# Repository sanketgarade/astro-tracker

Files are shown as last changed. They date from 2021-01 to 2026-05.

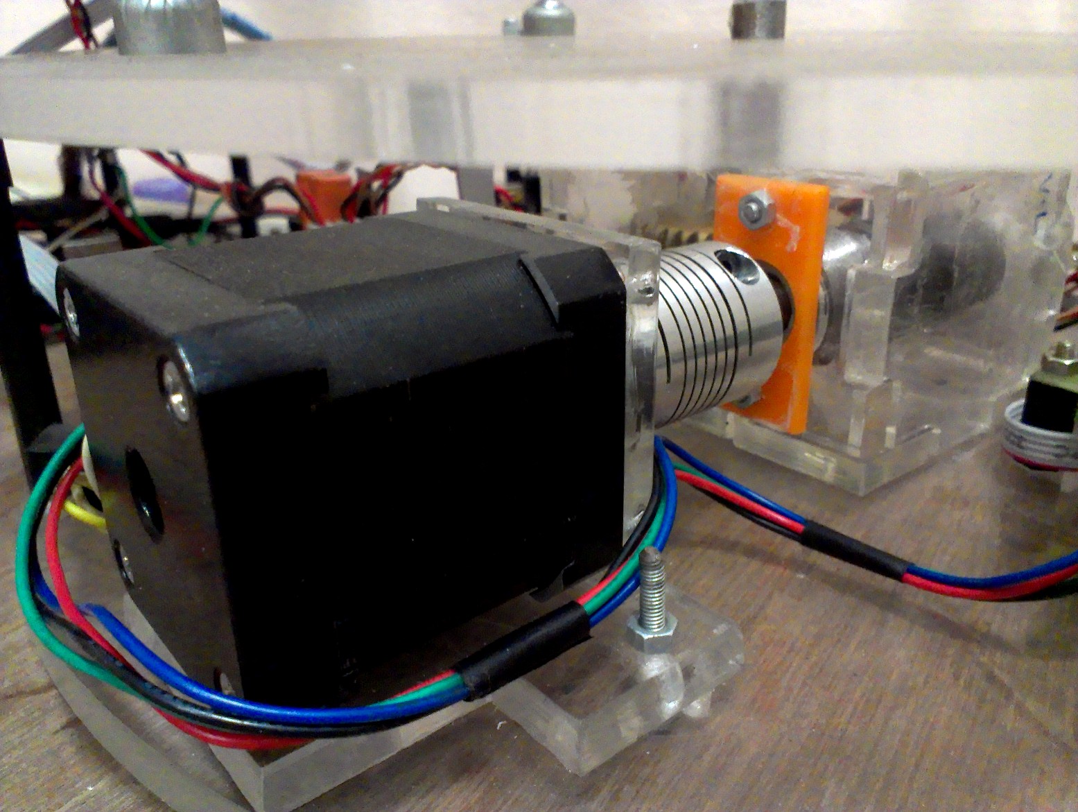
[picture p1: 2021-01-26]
Mechanical/Photos/H_01.jpg

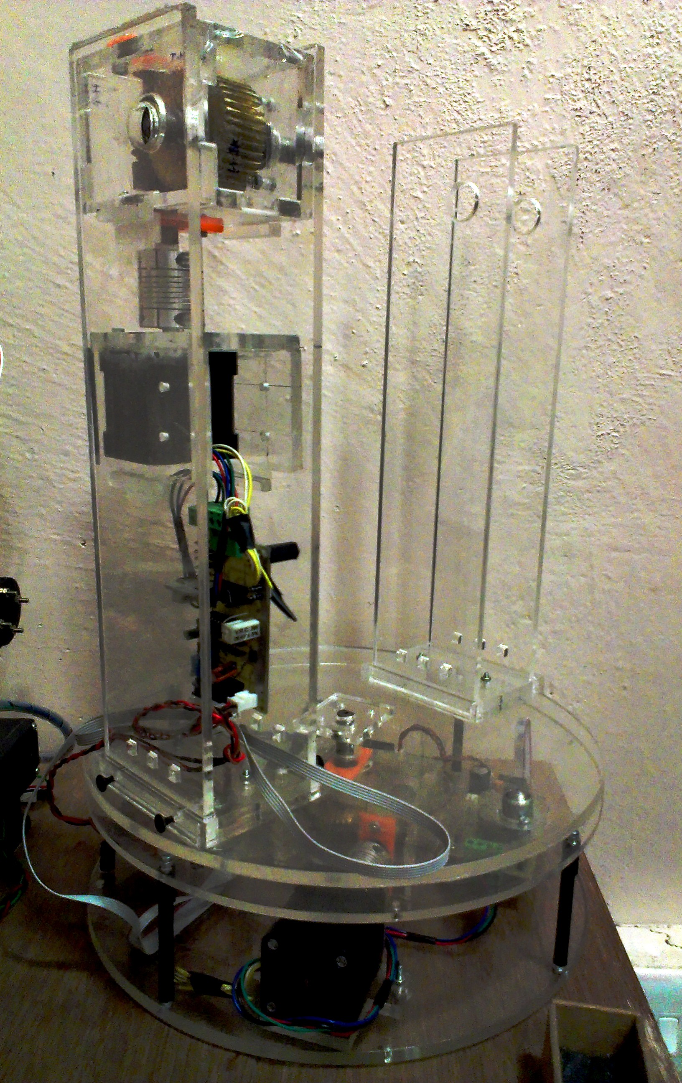
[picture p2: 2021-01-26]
Mechanical/Photos/Full.jpg

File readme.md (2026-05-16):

# Astro Tracker
## Computer controlled alt-az telescope mount

This is my M. Tech. Mechatronics project data. It was done in 2014-15.

Use the **Reports** folder to begin.

In other folders you can find all the documents and files for firmware code, hardware and mechanical CAD files, development plan etc.

## Some images/diagrams from the report are shown for a quick idea of the project



---



---



---



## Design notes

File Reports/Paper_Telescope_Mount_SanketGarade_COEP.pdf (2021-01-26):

## Design and development of computer controlled electro-mechanical mount for maneuvering an astronomical telescope

Mr. Sanket Garade | Prof. Dr. Rajiv B.
Department of Production Engineering and Industrial Management | Associate Professor, Department of Production Engineering and Industrial Management
College of engineering, Pune garadesp13.mecha@coep.ac.in | College of engineering, Pune rbh.prod@coep.ac.in

Abstract – It is essential requirement in area of astronomical research to develop a machine (known as alt-az mount) with which it will be helpful to track and view astronomical objects. This mount will be helpful in maneuvering a telescope and controlling it to point to the desired object in the sky. A computer software will send slew commands (for movement) to the mount which will in turn maneuver the telescope using electronic motors and mechanical assembly of the mount. The mount can be operated in 2 modes – Normal and Scanning. In Normal mode, the mount will simply move the telescope according to the arrow keys (up/down/left/right) selected on the software. In Scanning mode, the telescope will perform a line by line scan of the area of the sky selected in the software.

Keywords – telescope, mount, alt-az, stepper motor, worm gears

I. INTRODUCTION
A. Telescope
A telescope is an instrument that gathers light and focuses that light into an image. In turn, this image can be magnified for viewing. A telescope is mounted in such a way that allows you to swing it freely from one object to another in the sky.
An astronomical telescope is used to observe celestial objects such as planets, stars, deep-sky-objects such as galaxies, nebulae, comets etc.
B. Telescope Mounts
Telescope mounts come in various types. The most two common types are equatorial mounts and alt-az (altitude-azimuth) mounts.
Equatorial mounts are more complex to design but are ideal for astronomical viewing as it allows movement aligned to the celestial objects i.e. about the polar axis.
Alt-az mounts are comparatively simpler to design and are primarily meant for terrestrial viewing. However these mounts are also used for astronomical viewing. The mount discussed in this paper is an alt-az mount.
C. Need of an automated mount
- An automatic mount facilitates fast navigation of the night sky when doing night sky observations.
- Compared to manual navigation of the telescope, an automatic mount requires less physical efforts as well, which can be very higher especially when using heavier telescope (larger than 8 inch scopes)
- In cold regions, staying out in the cold for an entire night doing observations can be a problem. In such cases, the observation can be done by sitting inside a room and controlling the scope using a computer.
- For long exposure photographic observations, a mount is used to avoid star trails which occur due to the rotation of the earth.
- Sky survey is done by many amateur astronomers around the world. In this, they scan an area of the sky looking for possibly new comets/meteors etc. This scanning can be done with minimum efforts when using a automated mount.

II. REQUIREMENT SPECIFICATIONS

- Load specifications: The mount must be able to maneuver a telescope which is maximum 1kg in weight and has maximum dimensions: length = 18 inches and diameter =

### 3 inches

- Performance specifications: The mount should have an angular resolution of 0.1°.
- Power specifications: The mount must be powered by 12v dc voltage either through a power supply or a battery.
- Dimensions: the mount (excluding the telescope) must fit in a box of 30cm x 30cm x 60cm.
- Communication specifications: It should communicate with an external device like PC/laptop over serial port. This communication will be used to carry the motion commands and information from PC to the mount and vice versa.

III. METHODOLOGY
The entire system will be as shown in the block diagram (Figure 1). The computer will be the master of the system and will issue commands to the electronic control board. This board will accordingly drive the stepper motors using the motor driver boards. The stepper motors will be connected to the gear boxes which will finally cause the motion of the 2 axes of the mount. The 2 axes will be vertical and horizontal,

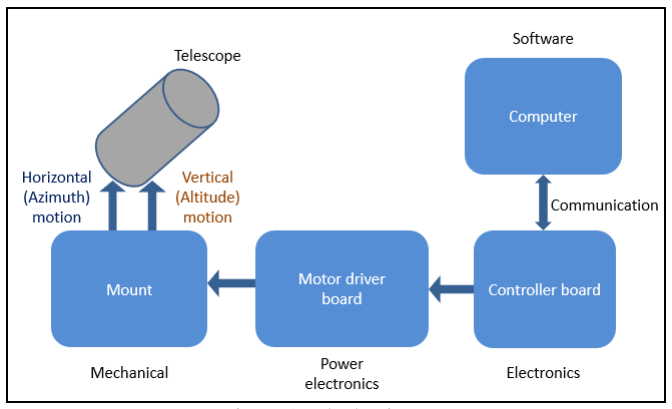
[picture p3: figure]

Figure 1- Block Diagram

known as altitude and azimuth axes respectively in astronomical terms. Hence the mount is also called an “alt-az” mount.

Each gear box contains 1 worm and worm-wheel gear set. The worm is driven by a stepper motor having step angle 0.9°. The worm-wheel is connected to the load. In case of azimuth motion, the load is the horizontal turn-table (red colour in Figure 3) along with the attached telescope. In case of altitude motion, the load is the telescope.

III. OPERATING MODES

The mount will be operated in 2 modes – Normal and Scanning. Overview of the same in shown in Figure 2.

A. Normal mode
In this mode, the telescope will be simply moved up/down/left/right using the arrows keys on the software. The resolution of the movement can also be controlled from the software. Lesser resolution will be used in moving the telescope from one point to another when the points are far away. This will help is faster movement. On the other hand, higher resolution will be used to perform very small changes in the telescope’s position. This will result in slower but fine control when pin-pointing to objects in the field of view of the telescope.
B. Scanning mode
In this mode, the telescope will be used to scan a particular region of the sky. This kind of scanning activity, performed by amateur astronomers, is called “sky survey”. Sky surveys result in observing and finding new celestial objects such as comets.
In this mode, the arrow keys will be used to position the scope to a desired start point in the sky. Then, the area to be scanned (e.g. 5° x 3°) will be entered along with the desired quadrant.
On pressing the “Zero” button, the mount will begin line-by-line scan of the selected quadrant and will cover the selected area of scan. The scan will be performed in a pattern where the scope will traverse the horizontal dimension first (i.e. 5°) and move up/down in a small vertical increment of 0.5° (fixed). It will again cover the horizontal distance followed by another vertical increment and keep on doing this till the vertical dimension (3°) is fully covered.

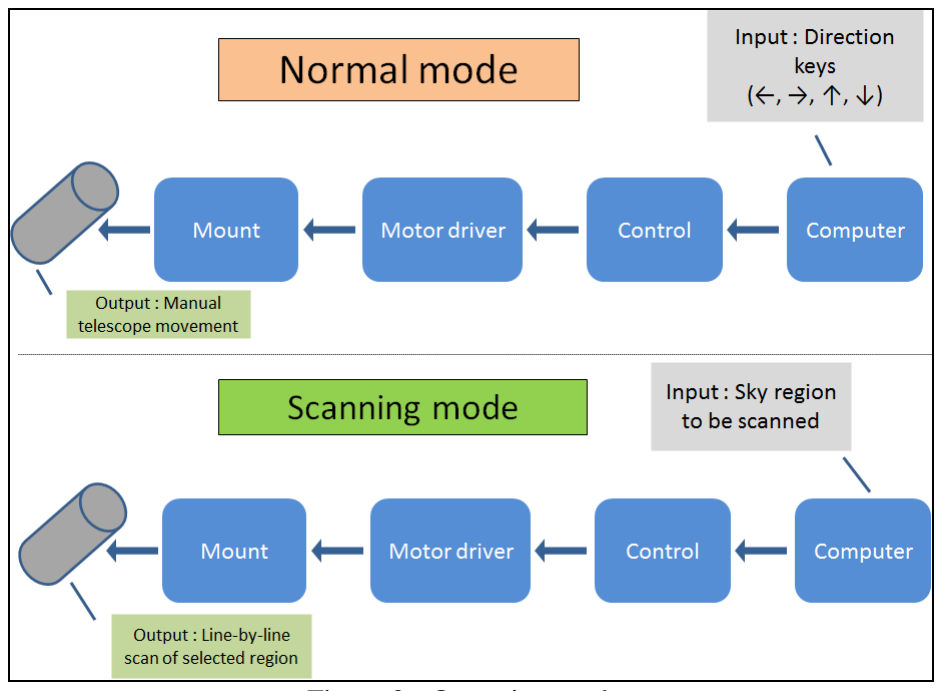
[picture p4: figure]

Figure 2 - Operating modes

The speed of scanning can also be selected from the software before beginning the scan.

IV. DESIGN

The design of the mount system is split into 3 parts each of which is given below.

A. Mechanical design
The mount is divided 2 sections according to the drive direction – Horizontal drive (blue) and vertical drive (red). The horizontal drive is enclosed in the base of the mount. It drives the turn-table on which the vertical dive assembly rests. The vertical drive assembly consists of 2 pillars. One pillar houses the vertical drive whereas the other acts as a support to the telescope. Both these pillars have coinciding shafts which protrude out to connect to the telescope.

The 3D model of the mount is developed using CATIA V5 software.

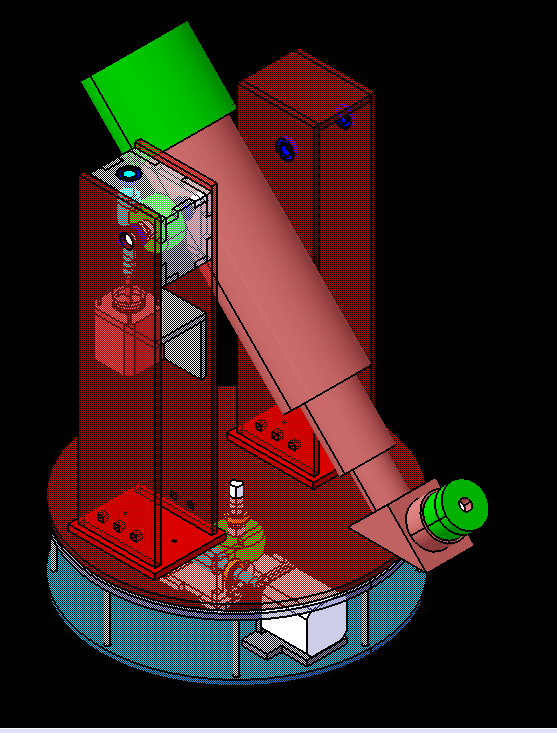
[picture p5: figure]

Figure 3 - Designed model of the alt-az mount with the telescope

Both the drives have similar construction. Each drive consists of – stepper motor, coupling, worm-wheel gears and bearings. The stepper motor shaft is connected to the worm shaft through an encoder coupling. The worm gear is made from EN-8 mild steel and the worm-wheel is made from Phosphor-Bronze material. The gears are assembled in a housing made of 6mm thick acrylic sheets. 10mm inner diameter ball bearings are used to support the gear shafts.

B. Electronic design
The electronics module consists of a control board and 2 motor driver boards.
The control board takes commands from the PC over the serial port and in turn gives drive signals to the driver boards. It also sends back to the PC status of the controller and other information. The control board uses an ATMega32 micro-controller.
Two driver boards are used, one for each drive. The driver board uses a L297 IC as the stepper motor controller. It receives the driving clock pulses and other control signals from the control board. Depending on this, it issues the winding sequences according to the selected step mode and direction. The winding sequence is given to the driver IC L298N which has a H-bridge driver within. The motor’s four windings are connected to the four outputs of the L298N in a bipolar motor configuration.
A stepper motor with 0.9° step angle is used as a prime mover. It is used in full step mode to maximize the torque output. The motor is of a standard NEMA 17 size.
The control board also has a failsafe feature wherein it stops the mount operation in case of a communication failure, i.e. if there is no communication received from the PC for a timeout period of 2 seconds.

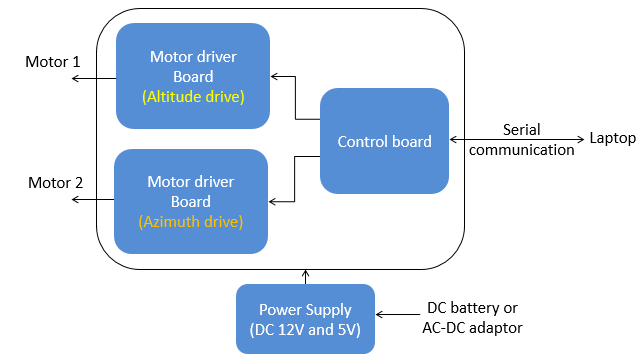
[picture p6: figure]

Figure 4 - Electronic design - block diagram

The schematic and board layout is designed using ExpressSCH and ExpressPCB software respectively.
The entire electronics is powered from a 12V DC power supply adapter.
C. Software design
The screenshot of the developed software is shown in Figure 5. This software application is used to control the telescope in both the operating modes.
To start, the COM port of the PC is selected from the drop down menu. The “Connect” button is used to connect to the selected COM port and then “Start” button is pressed. Default selected mode is “Normal”. The arrow keys in the “Normal” frame can be used to the move the telescope in the respective directions.

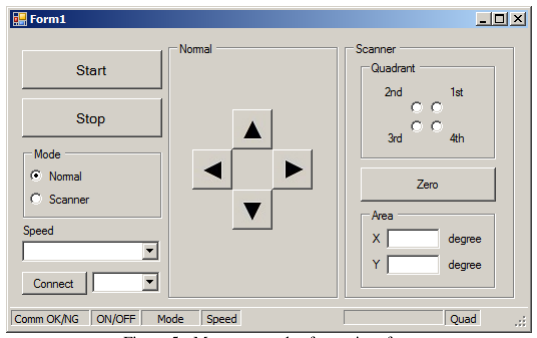
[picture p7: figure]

Figure 5 - Mount control software interface

By selecting “Scanner” button, the mount enters the scanning mode. Here it needs to be brought to an initial position using the four arrow keys. Once the initial position is set, the Quadrant and Area is set and scanning can be started by pressing the “Zero” button. Once scanning has started, the arrow keys cannot be used till the scanning is complete. If it is needed to stop scanning at anytime, the “Stop” button can be used to do the same.

The status strip at the bottom of the window gives various statuses received from the mount’s electronic control board. The software application has been developed in Microsoft Visual Studio using C# language.

V. CONCLUSION
An alt-az telescopic mount was successfully designed and developed from scratch. The developed mount was able to achieve the targeted system requirements such as 1Kg load and 0.1° angular resolution. It is working correctly as per the designed operating modes and their controls. The failsafe feature is also working as expected and stops the mount in case of communication failure.

VI. REFERENCES

Permanent Magnet Motor Technology – Jacek F. Gieras

http://www.celestron.com/support/knowledgebase

http://ascom-standards.org/

http://www.skyatnightmagazine.com/

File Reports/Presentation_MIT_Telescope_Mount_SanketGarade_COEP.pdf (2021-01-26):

# Design and development of a computer controlled electro-mechanical mount for maneuvering an astronomical telescope

Sanket Garade
S.Y. M. Tech. Mechatronics College of Engineering, Pune

Presented at

### 6th National Conference on Multidisciplinary Research in Science and Engineering MIT Academy of Engineering, Alandi 2015 June 5th

# Introduction

- Telescope –
A telescope is an instrument that gathers light and focuses that light into an image. In turn, this image can be magnified. This instrument is also mounted in such a way that allows you to swing it from object to object.
An astronomical telescope is used to observe celestial objects such as planets, stars, deep-sky-objects such as galaxies, nebulae, comets etc.

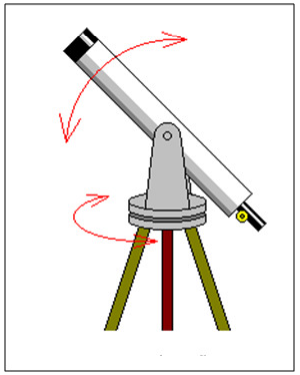
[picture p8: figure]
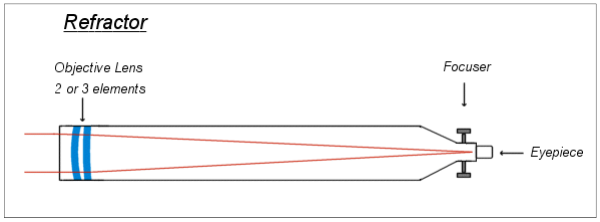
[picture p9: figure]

# Introduction

- | Celestial Co-ordinate systems – | A system for specifying positions of celestial objects.
- | Alt-az coordinate system – | In this system, the positioning of a celestial object varies with time, but is a useful
coordinate system for locating and tracking objects for observers on earth. – | It is based on the position of stars relative to an observer's ideal horizon. – | This system is not the best for astronomical purposes, but is still used by people as it is

simpler than the equatorial system.

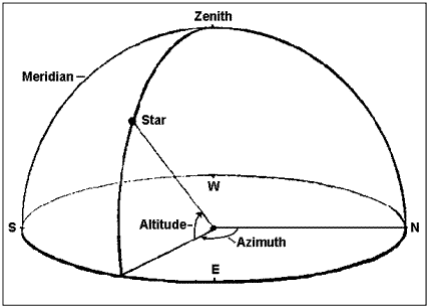
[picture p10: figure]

# Introduction

- | Equatorial coordinate system – | The equatorial coordinate system is centered at Earth's center, but fixed relative to
distant stars and galaxies. – | The coordinates are based on the location of stars relative to Earth's equator if it were
projected out to an infinite distance – | This system is popularly used for astronomical purposes, but it is more complex than the
| | alt-az system.

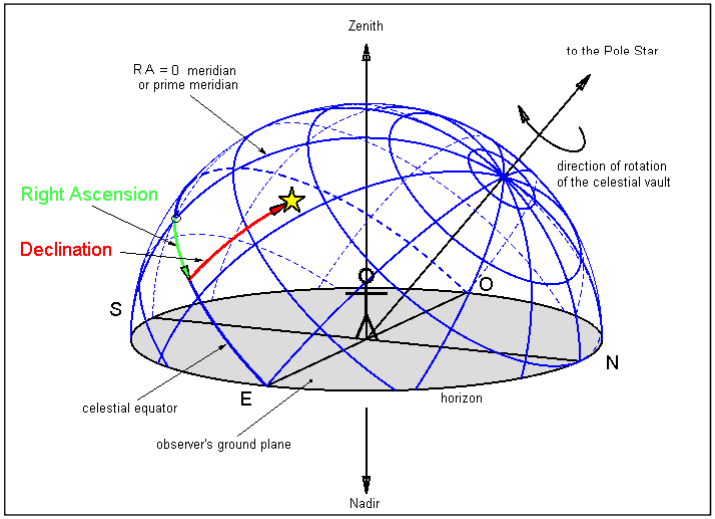
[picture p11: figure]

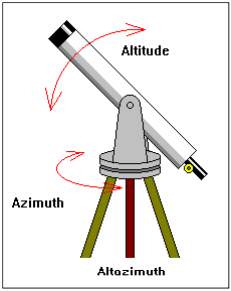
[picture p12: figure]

# Study of mount

### - Alt-azimuth mount (alt-az)

– | Simplest type of mount
– | It has 2 motions
| • Horizontal / Azimuth / Side to side • Vertical / Altitude / Up and down
– | Good for terrestrial observing and for scanning the
| sky at lower magnification.
– | Not good for deep sky photography.

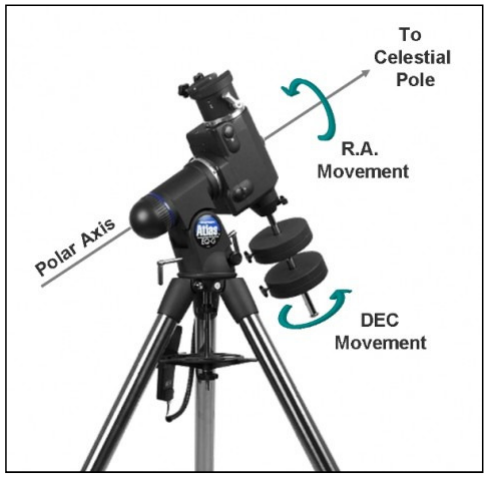
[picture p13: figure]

### - Equatorial mount (EQ)

– | Complex type of mount
– | It’s 1 axis is tilted such that it passes through
| the celestial pole (Pole star).
– | It has 2 motions
| • Right ascension (RA) – about the polar axis • Declination (DEC) – about an axis perpendicular to the polar axis
– | Best for astronomical observation and deep
| sky long exposure photography.

# Need for an automatic mount

- An automatic mount facilitates fast navigation of the night sky when doing night sky observations.
- Compared to manual navigation of the telescope, an automatic mount requires less physical efforts as well, which can be very higher especially when using heavier telescope (larger than

### 8 inches)

- Also in cold regions, staying out in the cold for an entire night doing observations can be a problem. In such cases, the observation can be done by sitting inside a room and controlling the scope using a computer.
- Also, for long exposure photographic observations, a mount is used to avoid star trails which occur due to the rotation of the earth.
- “Sky survey” is done by many amateur astronomers around the world. In this, they scan an area of the sky looking for possibly new comets/meteors etc. This scanning can be done with minimum efforts when using a automated mount.

# Problem statement

### - Problem Statement –

– | A machine (called “mount”) is to be built which can hold a telescope and can be controlled from a computer to point to a desired object in the sky.
– | It should do the following 2 tasks :-

### 1. In normal mode, the user should be able to maneuver the telescope using the direction

| control keys on the computer software.

### 2. In scanning mode, the area of the sky to be scanned will be given as input from the

| computer software. The mount will perform a line-by-line scan of the selected region of the sky. This technique is commonly used for sky survey activities by various astronomers.

### - Specifications –

– | Load specifications : The mount must be able to maneuver a telescope which is maximum 1Kg in weight and has max dimensions : Length = 18 inches and diameter = 3 inches
– | Performance specifications : The mount should provide an angular resolution of 0.1

°, at
| least, in both its’ axes.

# Block Diagram

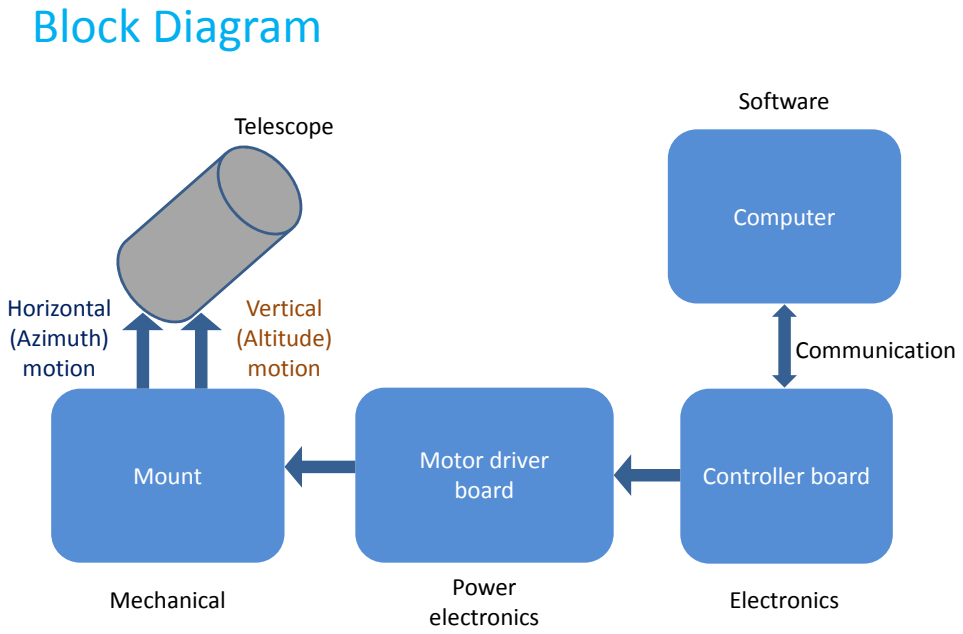
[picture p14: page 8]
Software; Computer; Telescope; Horizontal; Vertical; Mount; Motor driver board; Mechanical; Power electronics; Controller board; Electronics; (Altitude) motion; Communication; (Azimuth) motion

# Modes of operation

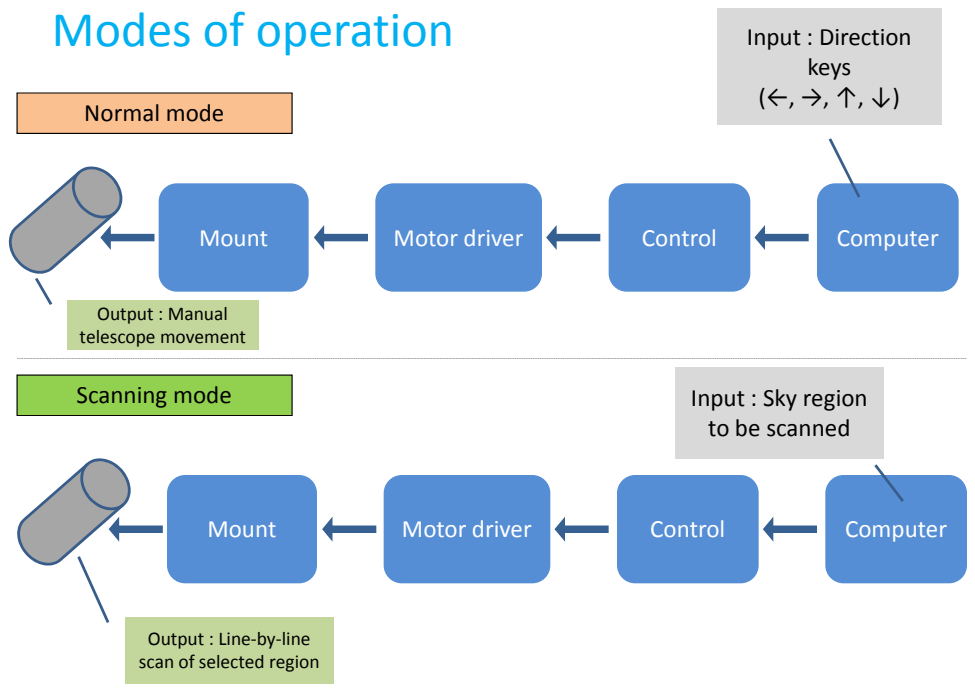
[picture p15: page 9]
Normal mode; Mount; Motor driver; Control; Computer; Output : Manual; Input : Direction keys (←, →, ↑, ↓); Scanning mode; telescope movement

Input : Sky region
to be scanned

Output : Line-by-line
scan of selected region

# Mechanical Design : Alt-azimuth mount

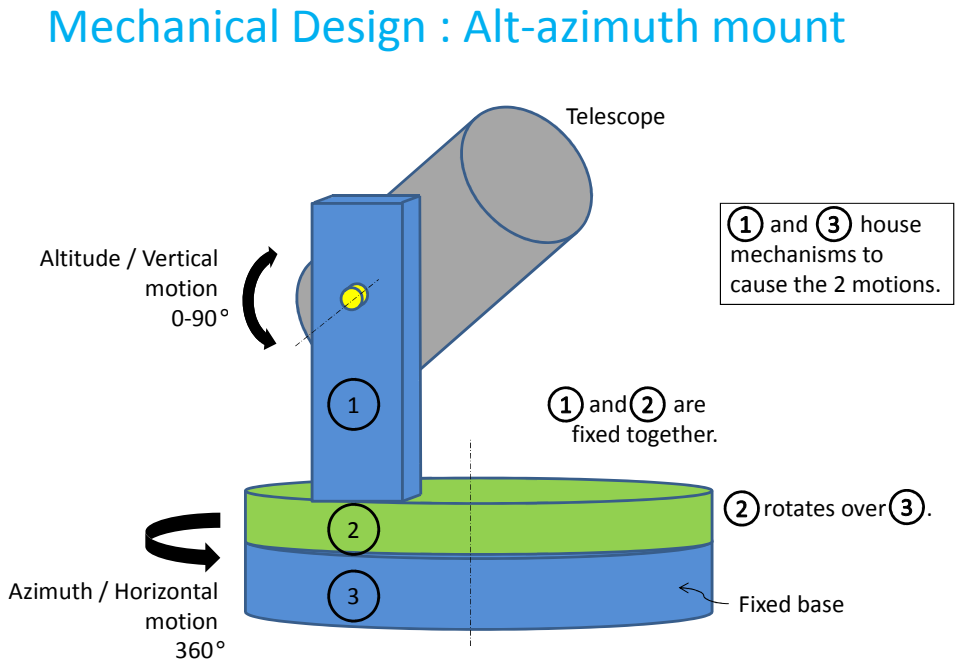
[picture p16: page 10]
Telescope; Altitude / Vertical motion 0-90 °; and; house; Azimuth / Horizontal motion; Fixed base; are; fixed together.; rotates over

mechanisms to
cause the 2 motions.

# Alt-azimuth mount : Internal components

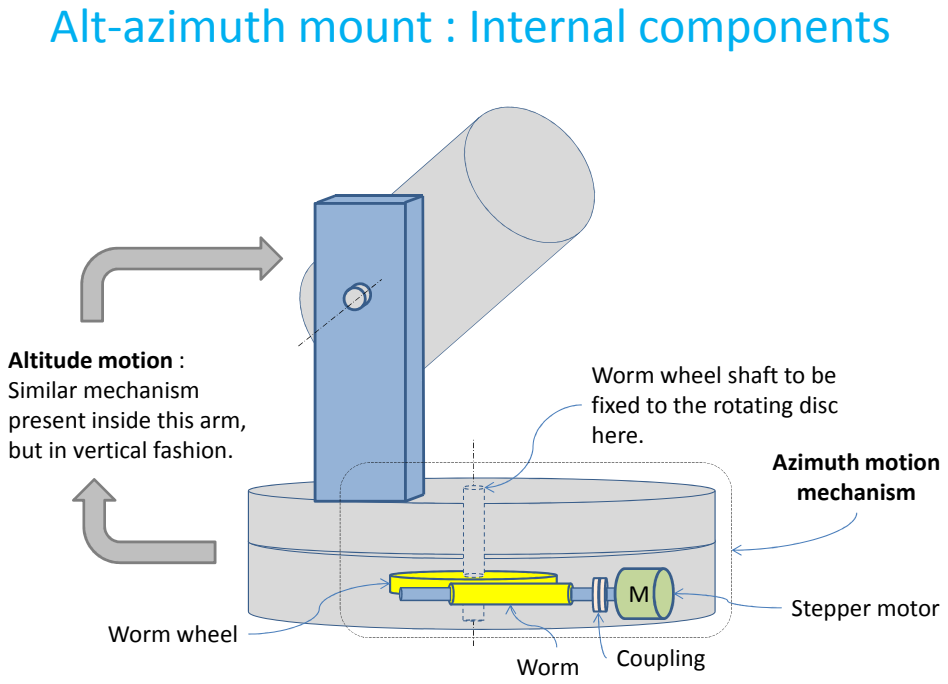
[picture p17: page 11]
Worm wheel; Worm; Stepper motor; Coupling; but in vertical fashion.; Azimuth motion; mechanism

Altitude motion :
Similar mechanism
present inside this arm,

Worm wheel shaft to be
fixed to the rotating disc
here.

# Mount Load calculations – Altitude motion

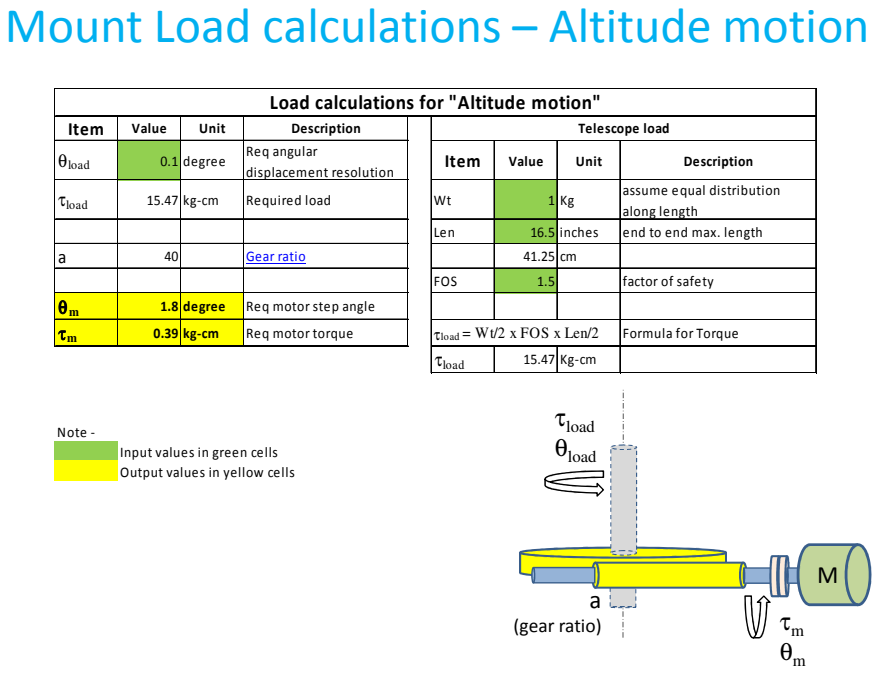
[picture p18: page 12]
Note -; τload; θload; (gear ratio)

Load calculations for "Altitude motion"

Item | Value | Unit | Description | Telescope load
θload | 0.1 | degree | Req angular displacement resolution | Item | Value | Unit | Description

τload | 15.47 | kg-cm | Required load | Wt | 1 | Kg | assume equal distribution along length

Len | 16.5 | inches | end to end max. length

a | 40 | | Gear ratio | | 41.25 | cm

FOS | 1.5 | | factor of safety

θ m | 1.8 | degree | Req motor step angle

τ m | 0.39 | kg-cm | Req motor torque | τload = Wt/2 x FOS x Len/2 | | | Formula for Torque

τload | 15.47 | Kg-cm

Input values in green cells
Output values in yellow cells

# Mount Load calculations – Azimuth motion

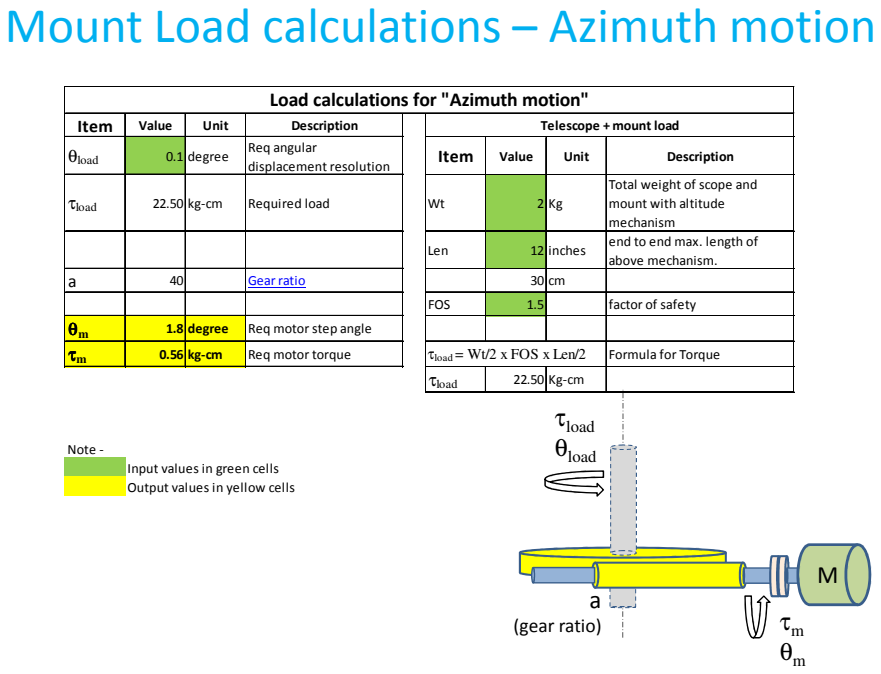
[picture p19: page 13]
Note -; τload; θload; (gear ratio)

Load calculations for "Azimuth motion"

Item | Value | Unit | Description | Telescope + mount load
θload | 0.1 | degree | Req angular displacement resolution | Item | Value | Unit | Description

τload | 22.50 | kg-cm | Required load | Wt | 2 | Kg | Total weight of scope and mount with altitude mechanism

Len | 12 | inches | end to end max. length of above mechanism.

a | 40 | | Gear ratio | | 30 | cm

FOS | 1.5 | | factor of safety

θ m | 1.8 | degree | Req motor step angle

τ m | 0.56 | kg-cm | Req motor torque | τload = Wt/2 x FOS x Len/2 | | | Formula for Torque

τload | 22.50 | Kg-cm

Input values in green cells
Output values in yellow cells

# Mount model

- The mount model is designed using CATIA V5 software.
- | Part design is divided into following – – | Worm and wheel gears – | Motor, Couplings, Bearings – | Motor clamps and gear housings – | Bottom frame and vertical frames – | Supporting plates
- | Assembly is done in following stages – – | Gear and housing assembly – | Motor and coupling with gears – | Horizontal drive – | Vertical drive – | Telescope attachment

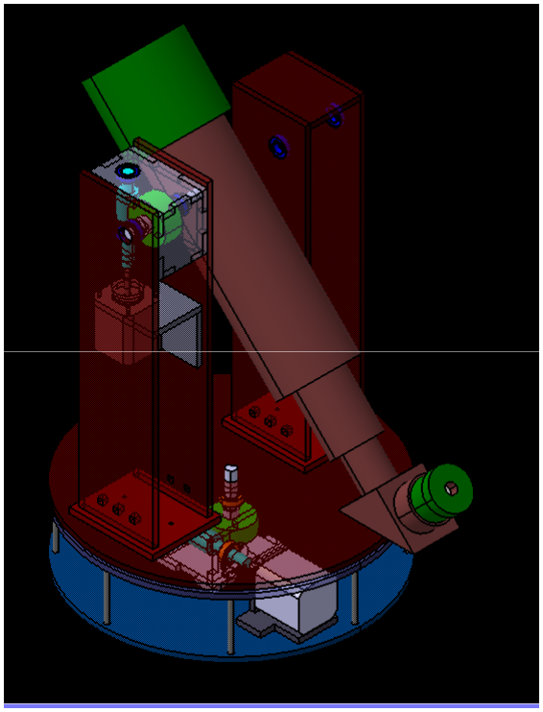
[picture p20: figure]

3D model of telescope mount

# Mount model

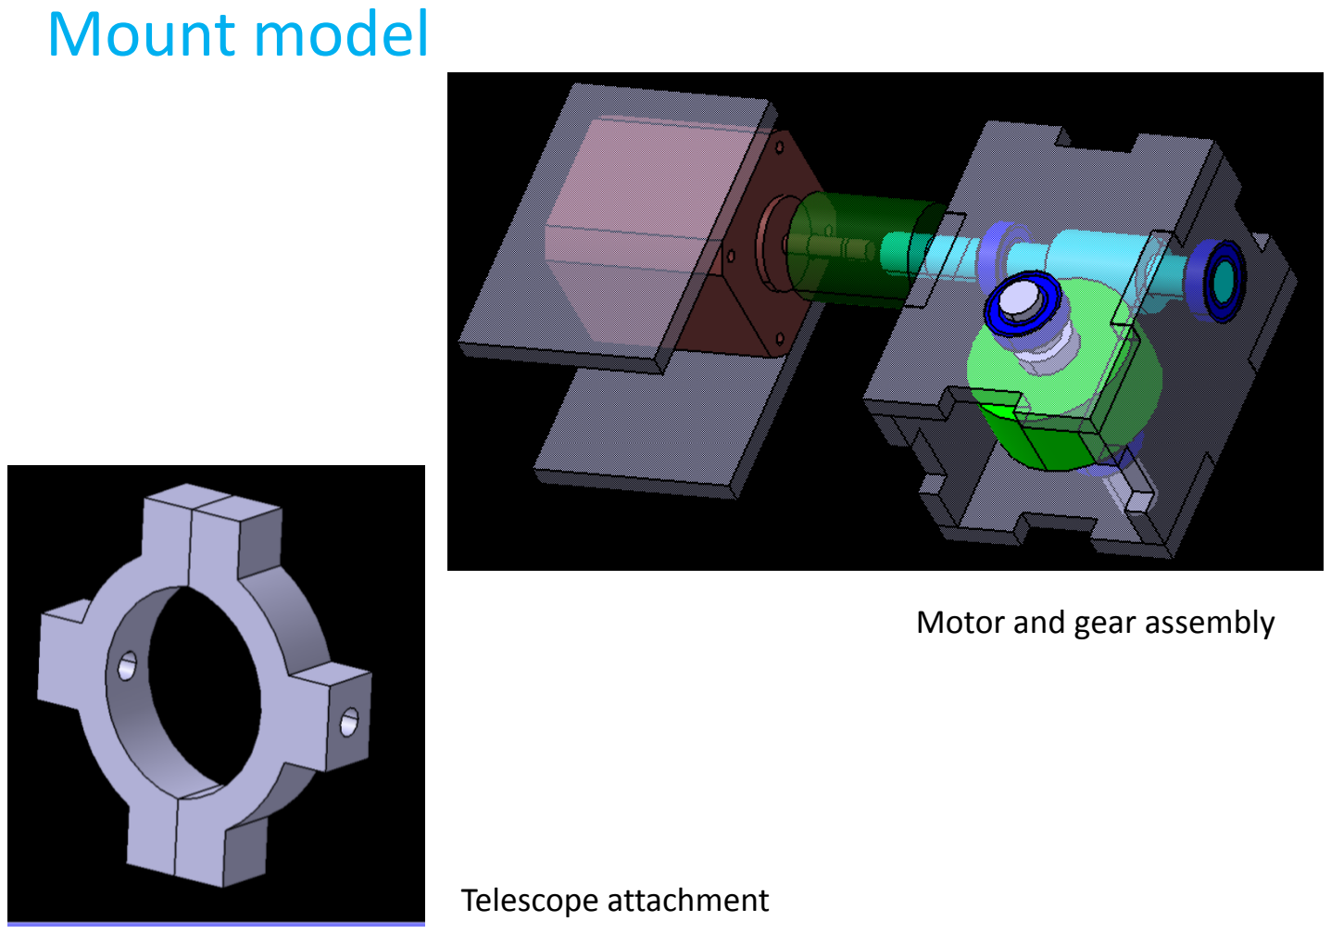
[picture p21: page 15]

Telescope attachment

Motor and gear assembly

# Mount model

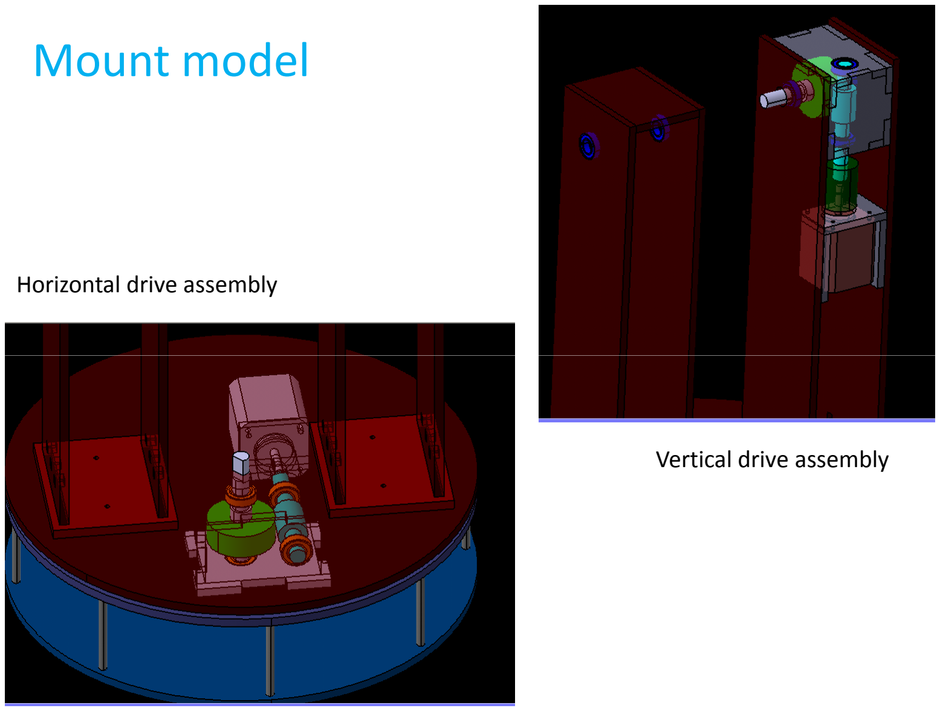
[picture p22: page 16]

Horizontal drive assembly

Vertical drive assembly

# Mount photos

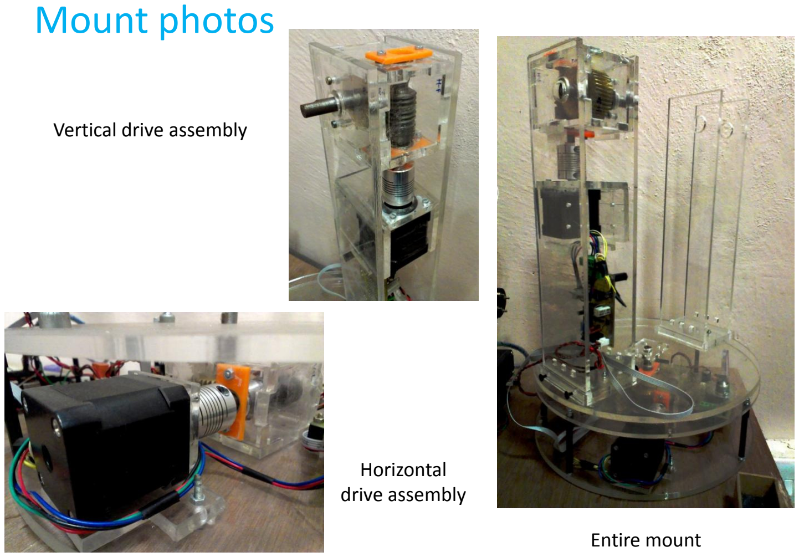
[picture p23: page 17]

Vertical drive assembly

Horizontal
drive assembly

Entire mount

# Electronic Design

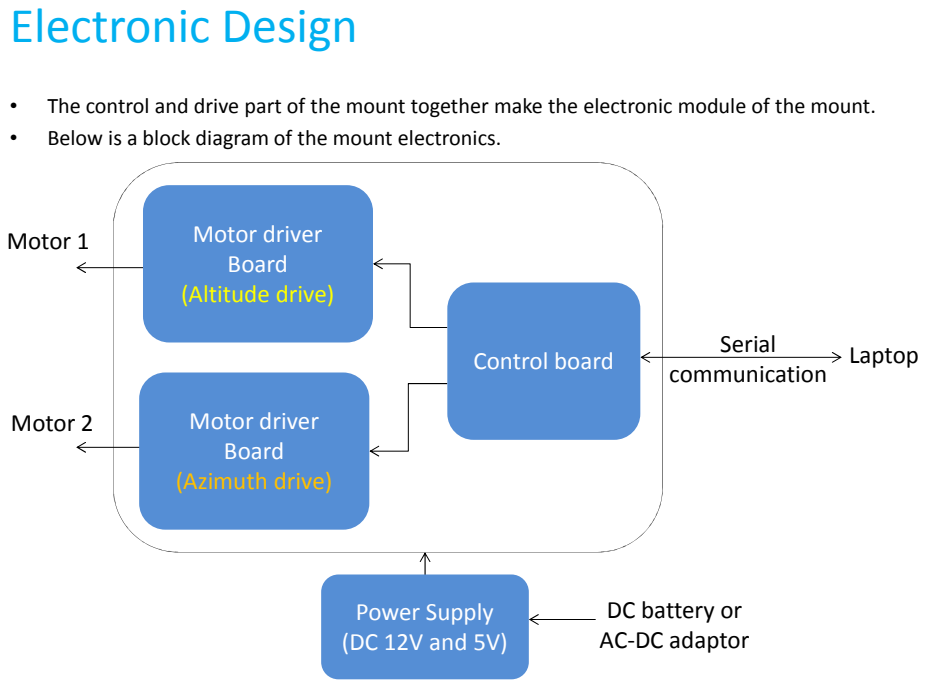
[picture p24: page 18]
Motor driver Board (Altitude drive); Motor 1; Serial; communication Control board; Laptop; Motor driver Board (Azimuth drive); Power Supply (DC 12V and 5V); Motor 2

• The control and drive part of the mount together make the electronic module of the mount.
• Below is a block diagram of the mount electronics.

DC battery or
AC-DC adaptor

# Electronic Design – Motor driver

- The motor driver mainly consists of the following components:-
– | Stepper motor controller (IC L297) - For stepper motor sequencing
– | H bridge driver (IC L298) | - For motor driver
- The stepper motor selected is 4209L-03 motor as shown below:
– | Step size = 0.9°
– | NEMA Standard 17 size

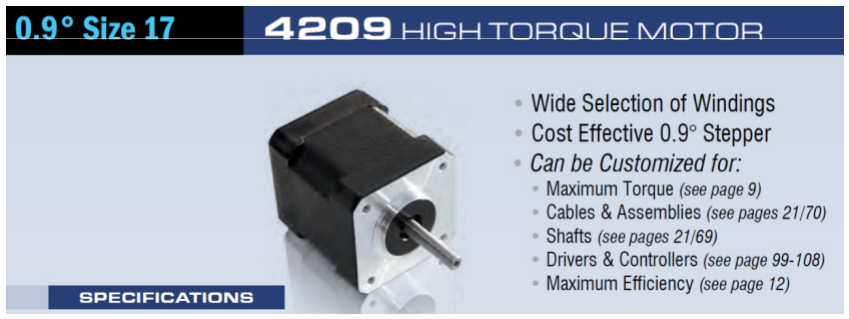
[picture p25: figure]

# Electronic Design – Schematic

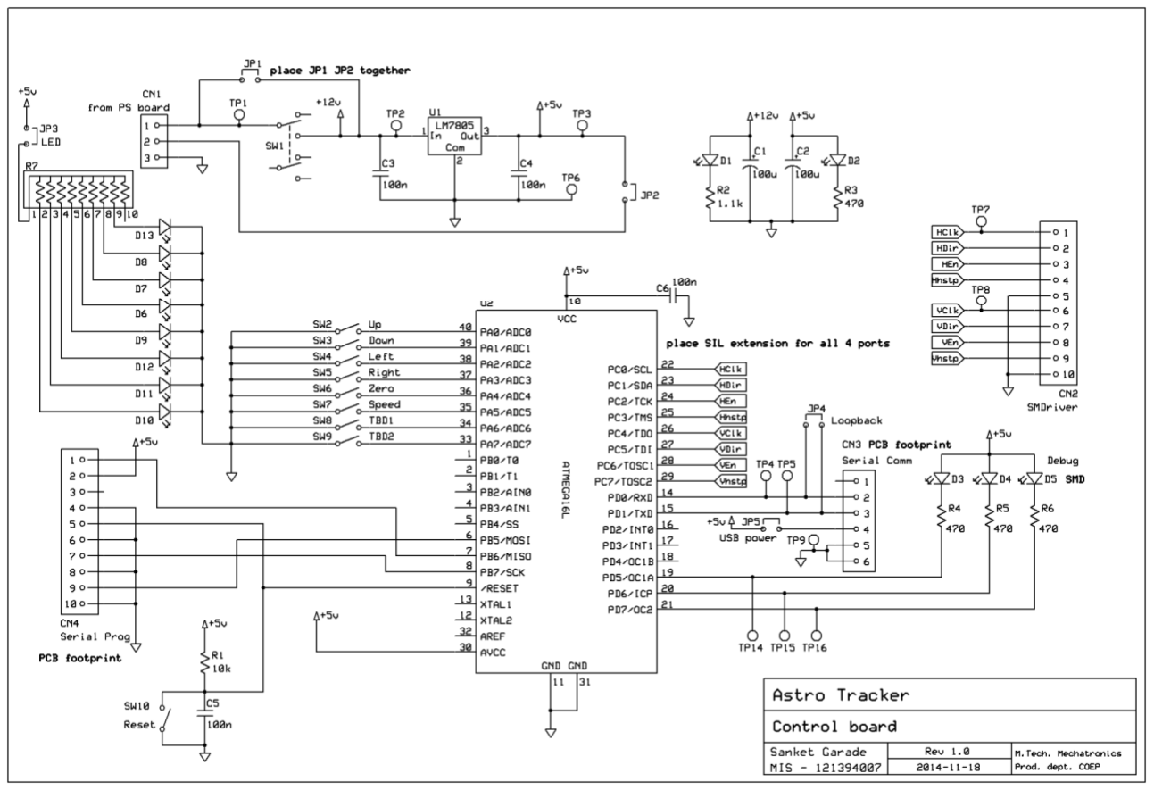
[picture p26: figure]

- SCH – Control board

# Electronic Design – Schematic


- SCH – Stepper Motor driver

# Electronics Design – Firmware

- The firmware architecture is shown below.
- It incorporates 3 separate tasks –
- Background job (lowest priority)
- Serial reception interrupt (intermediate priority)
- Timer interrupt (highest priority)


# Communication Design

- The communication between the computer software and the control board will be done using serial communication (UART)
- A communication protocol is designed which will be used to carry the information.

Communication
Interface
- The communication interface is designed in such a way that it ensures that the received data is valid and error free. This is done by implementing checksum logic.
- Also if either entity does not receive communication from other entity, it indicates communication error.

# Software Design

- Windows application developed in Visual Studio 2010
- Issues commands to the mount control board via serial communication
- Displays various statuses of the mount controller in the status bar


Control software – Application Window

# Conclusion

- An alt-az telescopic mount was designed, developed and tested successfully.
- It was able to achieve the targeted system requirements such as 1Kg load and 0.1° angular resolution.
- It is working correctly as per the designed operating modes and their controls.

communication failure.

# Thank you

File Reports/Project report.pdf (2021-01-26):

## “Design and development of a computer controlled

## electromechanical mount for maneuvering a telescope”

### Submitted in partial fulfillment of the requirements

### of the degree of

### Master of Technology in Mechatronics

by

### SANKET PANDIT GARADE

### [MIS No. 121394007]

Guide:

PROF. DR. RAJIV B.

Associate Professor, Production Engg. Dept.

College of Engineering, Pune

Department of Production Engineering and Industrial Management

College Of Engineering Pune

June 2015

## ACKNOWLEDGEMENT

I owe thanks to many people who have helped and supported me during the various

phases of this project.

I give my deepest thanks to Prof. Dr. Rajiv. B., the guide of the project, for guiding

and correcting various details and documents of mine with attention and care. He has taken

the pain to go through the project and guide me correctly as and when needed.

I express my sincere thanks to Prof. Dr. Rajhans N. R. the Head of Production

Engineering Department, College of Engineering, Pune for extending her support.

My deep sense of gratitude to Prof. Dhanvijay, the Associate Professor ,Production

Engineering, College Of Engineering, Pune for his support & guidance.

I would also like to thank Apeksha madam, Fab. Lab. incharge for guiding and

allowing me to use the facilities in the lab which helped a lot. I would also like to thank my

institution and my faculty members without whom this project would have been a distant

reality. I also extend my heartfelt thanks to my family, friends and well-wishers.

Date: | Sanket Garade

## CERTIFICATE

This is to certify that the Dissertation entitled “Design and development of a

computer controlled electromechanical mount for maneuvering a telescope” submitted

by Sanket Garade MIS No. 121394007 in partial fulfillment of the requirement for the

award of the Degree of Master of Technology in Mechatronics of College of Engineering,

Pune affiliated to Savitribai Phule Pune University, is a record of his own work.

Prof Dr. Rajiv B. | Prof. Mrs. Dr. Rajhans N. R.
Guide | Head of Department
Department of Production Engg. | Department of Production Engg.
College of Engineering, Pune. | College of Engineering, Pune.

Date:

Place: Pune

Dissertation Approval for M. Tech.

This dissertation entitled

DESIGN AND DEVELOPMENT OF A COMPUTER CONTROLLED ELECTROMECHANICAL MOUNT FOR MANEUVERING A TELESCOPE

By

Sanket Pandit Garade

(MIS no. 121394007)

is approved for the degree of

Master of Technology with specialization in Mechatronics

of

Department of Production Engineering and Industrial Management

College of Engineering Pune

(An autonomous institute of Govt. of Maharashtra)

Examiners | Name | Signature
1. External Examiner | ____________________________
2. Internal Examiner | ____________________________
3. Supervisor (s) | ____________________________
| ____________________________

Date:

Place: Pune

## Declaration

I declare that this written submission represents my ideas in my own words and where others'

ideas or words have been included, I have adequately cited and referenced the original

sources. I also declare that I have adhered to all principles of academic honesty and integrity

and have not misrepresented or fabricated or falsified any idea/data/fact/source in my

submission. I understand that any violation of the above will be cause for disciplinary action

by the Institute and can also evoke penal action from the sources which have thus not been

properly cited or from whom proper permission has not been taken when needed.

______________________

Sanket Pandit Garade

MIS No. 121394007

Date:

Place: Pune

## ABSTRACT

It is essential requirement in area of astronomical research to develop a machine (known as a

mount) with which it will be helpful to track and view astronomical objects. The purpose of

this dissertation is to develop such a mount which will be of help amateur astronomy

enthusiasts. It will help in maneuvering a telescope and controlling it to point to the desired

object in the sky. The control will be done from software running on a computer connected to

this mount. Computer software will send slew commands (for movement) to the mount which

will in turn maneuver the telescope using the electronic motors and mechanical assembly of

the mount. The mount can be operated in 2 modes – Normal and Scanning. In Normal mode,

the mount will simply move the telescope according to the arrow keys (up/down/left/right)

selected on the software. In Scanning mode, the telescope will perform a line by line scan of

the area of the sky selected in the software.

TABLE OF CONTENTS

LIST OF FIGURES

LIST OF TABLES

LIST OF ABBREVIATIONS

Alt-az | - | Altitude-Azimuth
EQ | - | Equatorial
HW | - | Hardware
FW | - | Firmware
SW | - | Software
PCB | - | Printed circuit board

## 1. Introduction

## 1.1. Background

### 1.1.1. Telescope

A telescope is an instrument that gathers light and focuses that light into an image. In

turn, this image can be magnified for viewing. A telescope is mounted in such a way that

allows you to swing it freely from one object to another in the sky.

An astronomical telescope is used to observe celestial objects such as planets, stars,

deep-sky-objects such as galaxies, nebulae, comets etc.

### 1.1.2. Telescope Mounts

The mechanism which supports the telescope and is used to maneuver it is called a

mount. Mounts come in various types. The most two common types are equatorial mounts

and alt-az (altitude-azimuth) mounts.

Equatorial mounts are more complex to design but are ideal for astronomical viewing

as it allows movement aligned to the celestial objects i.e. about the polar axis.

Alt-az mounts are comparatively simpler to design and are primarily meant for

terrestrial viewing. However these mounts are also used for astronomical viewing. The mount

designed in this project is an alt-az mount.

### 1.1.3. Need of an automated mount

- An automatic mount facilitates fast navigation of the sky when doing night sky

observations.

- Compared to manual navigation of the telescope, an automatic mount requires less

physical efforts as well, which can be very high especially when using heavier

telescope (larger than 8 inch scopes)

- In cold regions, staying out in the cold for an entire night doing observations can be a

problem. In such cases, the observation can be done by sitting inside a room and

controlling the scope using a computer.

- For long exposure photographic observations, a mount is used to avoid star trails

which occur due to the rotation of the earth.

- Sky survey is done by many amateur astronomers around the world. In this, they scan

an area of the sky looking for possibly new comets/meteors etc. This scanning can be

done with minimum efforts when using a automated mount

## 1.2. Aim and scope of project

The one line aim of the project is to –

Build a device (mount) which can be used to maneuver a telescope and point it to the desired object in the sky.

The detailed problem statement, scope of work and the requirement specifications are explained below.

### 1.2.1. Problem statement

A mount is to be built which can hold a telescope and can be controlled from a computer to

point to a desired object in the sky. It should operate in two modes:-

– In the Normal mode, the user should be able to maneuver the telescope

through the arrow keys on the computer software.

– In the Scanning mode, it should perform a line by line scan of the area of the

sky selected in the software.

### 1.2.2. Scope of work

Following table shows the different modules of the project and the scope of work in each.

Module | Scope of work
Electronics hardware and firmware - Power supply - Remote control - Motor driver | To be designed, implemented, integrated and tested.
Mechanical parts and assembly - Mount frame - Gears | To be designed, fabricated, assembled and tested.
Software - Stellarium (Astronomy software) | To be used as it is with minor modifications in the backend script.
Communication (between remote control and Stellarium) | To be implemented, integrated and tested.
Telescope | To be procured and integrated with the mount.

Table 1: Scope of work

### 1.2.3. Requirement specifications

Following are the technical requirement specifications of the project.

1. Load specifications: The mount must be able to maneuver a telescope which is

maximum 1kg in weight and has maximum dimensions: length = 18 inches and

diameter = 3 inches

2. Performance specifications: The mount should have an angular resolution of 0.1°.

3. Power specifications: The mount must be powered by 12v dc voltage either through a

power supply or a battery.

4. Dimensions: the mount (excluding the telescope) must fit in a box of 30cm x 30cm x

60cm.

5. Communication specifications: It should communicate with an external device like

PC/laptop over serial port. This communication will be used to carry the motion

commands and information from PC to the mount and vice versa.

6. Functional specifications: It should operate in two modes, Normal and Scanning.

## 2. Literature study

To design a telescope mount, the basic of telescopes, celestial coordinate system and

telescope mounts is to be studied. This will help in designing the mount efficiently and

controlling in the best possible way.

## 2.1. Theory of telescopes

A telescope is an instrument that gathers light and focuses that light into an image. In

turn, this image can be magnified. This instrument is also mounted in such a way that allows

you to swing it from object to object.

A telescope's ability to gather light is dependent on:

Aperture: The larger the primary optics (the largest lens or mirror) the more light is captured.

Optical quality: The more reflective a mirror and the more a lens allows light to pass through

it, the more light is transmitted to your eye.

Collimation (alignment): Even if you have the best optics, if they are not properly aligned,

your light gathering capacity will be diminished.

Below diagram shows a basic telescope and how it focuses light.


Figure 1.00 : Basic telescope working

## 2.2. Theory of celestial coordinates

In astronomy, a celestial coordinate system is a system for specifying positions of celestial

objects: satellites, planets, stars, galaxies etc. Coordinate systems can specify a position in 3-

dimensional space, or merely the direction of the object on the celestial sphere.

There are 2 main types of celestial coordinate systems:

1. Alt-az coordinate system
2. Equatorial coordinate system

### 2.2.1. Altitude azimuth system

The horizontal, or altitude-azimuth (alt-az), system is based on the position of the observer on

Earth, which revolves around its own axis once per sidereal day (23 hours, 56 minutes and

4.091 seconds) in relation to the "fixed" star background. The positioning of a celestial object

by the horizontal system varies with time, but is a useful coordinate system for locating and

tracking objects for observers on earth. It is based on the position of stars relative to an

observer's ideal horizon.


Figure 2.00 : Coordinate system - Alt-az

### 2.2.2. Equatorial system

The equatorial coordinate system is centered at Earth's center, but fixed relative to

distant stars and galaxies. The coordinates are based on the location of stars relative to Earth's

equator if it were projected out to an infinite distance. The equatorial describes the sky as

seen from the solar system, and modern star maps almost exclusively use equatorial

coordinates.

The equatorial system is the normal coordinate system for most professional and

many amateur astronomers having an equatorial mount that follows the movement of the sky

during the night. Celestial objects are found by adjusting the telescope's or other instrument's

scales so that they match the equatorial coordinates of the selected object to observe.


Figure 3.00 : Coordinate system – Equatorial

## 2.3. Theory of telescope mounts

A telescope mount is a mechanical structure which supports a telescope. Telescope mounts

are designed to support the mass of the telescope and allow for accurate pointing of the

instrument. Many sorts of mounts have been developed over the years, with the majority of

effort being put into systems that can track the motion of the stars as the Earth rotates.

Functions of a telescope mount:

1. It should provide a system for smooth controlled movement to point and guide the

instrument.

2. It should support the telescope firmly so that you can view and photograph objects

without having the image disturbed by movement.

Main types of telescope mounts:

1. Alt-azimuth mounts (alt-az)
2. Equatorial mounts

### 2.3.1. Alt-az mount

An alt-az mount is the simplest type of mount. It has two motions, altitude (up and

down, vertical to the horizon) and azimuth (side-to-side, along the horizon). Good mounts

will have slow-motion knobs to make precise adjustments, which aid in keeping tracking

motion smooth. These mounts are good for terrestrial observing and for scanning the sky at

lower power but are not for deep sky photography. Certain alt-az mounts (GoTo mounts) are

now computer-controlled and allow a telescope to track the sky accurately enough for visual

use but are still not accurate enough for long exposure photography.

### 2.3.2. EQ mount

As the Earth rotates around its axis, the stars appear to move across the sky. If you are

observing them using an alt-az mount, they will quickly drift out of view. A telescope on an

equatorial mount can be aimed at a celestial object and easily track the daily motion, keeping

it in your eyepiece. It works by inclining it at an angle equal to your latitude and pointing one

axis (called either the polar axis or right ascension (RA) axis) in the same direction as the

Earth’s rotational axis (towards the celestial pole). Once the polar axis is parallel to the

Earth’s axis and turned at the same rate of speed as the Earth, but in the opposite direction,

objects will appear to stand still when viewed through your scope. There is no rotation of the

field of view and tracking can be extremely accurate, making the equatorial mount perfect for

astrophotography. It has two motions: in RA (east-west) and in declination (north-south).


Figure 4.00 : Telescope mount - types

## 3. Project Plan

The project activities and the schedule for the same are described below.

## 3.1. Activities

The project, being a mechatronics project and hence inter-disciplinary in nature, has a mix of various activities. These are listed below in brief:-

Main activity | Sub-activities
Study | Telescope and mount study
Electronics study – Stepper motor driving Mechanical study – Gear design, Assembly design

Electronics
Hardware
(HW)

Hardware design
Component selection
Component procurement
Bread board testing and redesign Schematic (SCH) design
PCB design
PCB manufacturing
Board assembly
Board bring up and testing

Electronics
Firmware
(FW)

FW test stubs
System architecture design Driver design
Application design
Implementation and testing

Mechanical
(Mount)

Load and torque analysis
Gear design
Gear manufacturing
Mount design
Mount manufacturing and assembly Mount testing and corrections
Software (SW) | Windows application development and testing
Integration and testing | Testing of electronics with mount
Final integration and testing
Other | Telescope selection and procurement
Table 2 : List of activities

21

## 3.2. Schedule

Below is the schedule for execution of the project.

Figure 5.00 : Project Schedule

## 3.3. Tools

Below is the list of tools and software required for the project execution:-

- Mechanical:
1. Catia | - For part design and assembly simulation
2. Epilog laser cutting machine - For manufacturing the mechanical parts
- Electronics:
1. Express SCH and PCB | - For schematic and PCB design
2. AVR studio | - For firmware design and implementation
3. Sinaprog | - For downloading firmware in the MCU
4. DMM and Oscilloscope | - For testing purpose
- Software:
1. Visual Studio 2010 | - For windows application development
2. Bray’s Terminal | - For testing serial communication

## 4. System Operation

This section gives the overview of the working of the mount.

## 4.1. System Overview

The mount comprises of the following blocks shown in the diagram.

In this arrangement,

The computer software is the “master”,

The mount is the “slave”.

And the telescope is the “load”.


Figure 6.00 : System block diagram

As can be seen from the block diagram, the system is an open loop system. i.e. no feedback is

given from the mount to the control board

## 4.2. Working of system

The system operation is described in this section. The system operates in 2 modes. Mode

selection can be done from the computer software window. Below are the details of the 2

modes.

### 4.2.1. Normal mode

In this mode, the telescope will be simply moved up/down/left/right using the arrows

keys on the software. The resolution of the movement can also be controlled from the

software. Lesser resolution will be used in moving the telescope from one point to another

when the points are far away. This will help faster movement. On the other hand, higher

resolution will be used to perform very small changes in the telescope’s position. This will

result in slower but fine control when pin-pointing to objects in the field of view of the

telescope.

### 4.2.2. Scanning mode

In this mode, the telescope will be used to scan a particular region of the sky. This

kind of scanning activity, performed by amateur astronomers, is called “sky survey”. Sky

surveys result in observing and finding new celestial objects such as comets.

First, the arrow keys will be used to position the scope to a desired start point in the

sky. Then, the area to be scanned (e.g. 5° x 3°) will be entered along with the desired

quadrant. On pressing the “Scan” button, the mount will begin line-by-line scan of the

selected quadrant and will cover the selected area of scan. The scan will be performed in a

pattern where the scope will traverse the horizontal dimension first (i.e. 5°) and move

up/down in a small vertical increment of 0.5° (fixed). It will again cover the horizontal

distance followed by another vertical increment and keep on doing this till the vertical

dimension (3°) is fully covered.

## 5. System Design

The system is divided into 4 parts for design purpose –

– | Mechanical design
– | Electronics design
– | Software design
– | Communication design

Each of these is explained in below sections.

## 5.1. Mechanical design

The high level mechanical design of the mount is shown in below diagram.

There will be 2 kinds of motions as shown –

1. Horizontal | OR | Azimuth motion
2. Vertical | OR | Altitude motion


Figure 7.00 : Mount design overview

Each of these motions/drives will be driven by a worm and worm-wheel gear. The reason for

choosing a worm drive for this application is because the angular resolution of the load is

very small (0.1°). As a worm gear has a very high reduction ratio, this accuracy can be

achieved along with satisfying the load torque.


Figure 8.00 : Mount design virtual section view

The worm gear will be driven by a stepper motor. Detailed calculations of the load are given

below.

### 5.1.1. Load calculations

The primary considerations for load are:-

1. Load torque (τload)
2. Load angular accuracy (θload) = 0.1° fixed.

Gear ratio (a) and motor (τm and θm) is to be selected to satisfy this load.


Figure 9.00 : Load consideration

Each of the 2 drives (altitude and azimuth) will have their own loads, details of which are

given below.

### 5.1.1.1. Altitude drive load

The load for the altitude drive is only the telescope. Hence only the telescope weight and

dimensions are used to determine the load torque in below calculations.

τload | 15.47 Kg-cm

Note -
Input values in green cells Output values in yellow cells
| Load calculations for "Altitude motion"
Item | Value | Unit | Description | Telescope load
θload | 0.1 degree | | Req angular displacement resolution | Item | Value | Unit | Description
τload | 15.47 kg-cm | | Required load | Wt | 1 Kg | | assume equal distribution along length
| | | | Len | 16.5 inches | | end to end max. length
a | 40 | | Gear ratio | | 41.25 cm
| | | | FOS | 1.5 | | factor of safety
θm | 1.8 degree | | Req motor step angle
τm | 0.39 kg-cm | | Req motor torque | τload = Wt/2 x FOS x Len/2 | | | Formula for Torque

Table 3 : Load calculation - Altitude drive

Thus, as can be seen, the load torque requirement is 15.47 kg-cm.

Considering a gear ratio of 1:40, a stepper motor having:-
Torque = 0.39 kg-cm at least and
Step angle = 1.8° maximum
should be selected for the “altitude drive”.

Note – Details of gear ratio selection is given in later section.

### 5.1.1.2. Azimuth drive load

The load for the azimuth drive is load of the telescope plus load of the mount frame. Hence

weight and dimensions of both are used to determine the load torque in below calculations.

Item | Value | Unit | Description | Telescope + mount load
θload | 0.1 | degree | Req angular displacement resolution | Item | Value | Unit | Description
τload | 22.50 | kg-cm | Required load | Wt | 2 | Kg | Total weight of scope and mount with altitude mechanism
| | | | Len | 12 | inches | end to end max. length of above mechanism.
a | 40 | | Gear ratio | | 30 | cm
| | | | FOS | 1.5 | | factor of safety
θm | 1.8 | degree | Req motor step angle
τm | 0.56 | kg-cm | Req motor torque | τload = Wt/2 x FOS x Len/2 | | | Formula for Torque
τload | 22.50 | Kg-cm
Note -
Input values in green cells
Output values in yellow cells

Load calculations for "Azimuth motion"

Table 4 : Load calculation - Azimuth drive

Thus, as can be seen, the load torque requirement is 22.5 kg-cm.

Considering a gear ratio of 1:40, a stepper motor having:-

Torque = 0.56 kg-cm at least and

Step angle = 1.8° maximum

should be selected for the “azimuth drive”.

### 5.1.2. Gear calculations

Each of the drives will be driven by a worm and worm-wheel gear. The reason for choosing a

worm drive for this application is because the angular resolution of the load is very small

(0.1°). As a worm gear has a very high reduction ratio, this accuracy can be achieved along

with satisfying the load torque.

A gear ratio of 40 was selected. Below is the calculation for the same.

Item | Value | Unit | Description
TG | 40 | | No. of teeth on gear "G"
TW | 1 | | No. of teeth/helix on worm "W"
a | 40 | | gear ratio (Tg/Tw)
θ1 | 1.8 degree | | Step angle of motor (assume)
θfull | 360 degree
| 200 | | No of motor steps per revolution of worm (θfull/θ1)
| 200 | | No of motor steps for displacing 1 tooth of Gear "G" (θfull/θ1)
Tx | 0.005 | | No of tooth of "G" displaced in 1 motor step (θ1/θfull)
θ2 | 9 degree | Angle displcement by displacing 1 tooth of "G" (θfull/a)
θload | 0.045 degree | Therefore, angle displcement by displacing Tx tooth of "G". Which is nothing but angle displaced of gear wheel "G" for 1 motor step. (θ1/a)
θload req | 0.1 degree | Required angluar resolution
Result | OK | OK - ok and valid design ; NG - not good.

Angular displacement Calculations

Gear (G)

Worm (W)

Stepper
Motor (M)

Enter a step angle such that value of θload (yellow) should come less than the max θload (red)

Enter values for gear
ratio. Use standard
gears.

Table 5 : Gear calculations

As can be seen, with this gear ratio, the required angular accuracy of the load can be easily

achieved.

### 5.1.3. Model design

The 3-D model of the mount was designed using CATIA v5 software. The parts were

individually designed in the part designer module and were assembled together in the

assembly module. The designed part files were used to fabricate the corresponding parts

using a laser cutting machine. Below are some of the screenshots of the 3-D model.

Also shown later are drawings and assembly stages of the mount.


Figure 10 : Mount 3-D model


Figure 11 : Drawing - Worm wheel

Figure 12 : Drawing - Worm


Figure 13 : Drawing - Base top plate


Figure 14 : Drawing - Vertical plate


Figure 15 : Assembly - Stage 1


Figure 16 : Assembly - Stage 2

## 5.2. Electronic design

The electronics design is divided in 2 parts – hardware and firmware.

### 5.2.1. Hardware design

The hardware design consists of 3 main parts as shown in below block diagram:-

1. Power supply
2. Control board
3. Stepper Motor Driver


Figure 17 : Electronic design - block diagram

### 5.2.1.1. Motor driver design

The motor driver mainly consists of the following components:-

1. Stepper motor controller (IC L297) | - For stepper motor sequencing
2. H bridge driver (IC L298) | - For motor driver

Schematic of the motor driver board is shown below.


Figure 18 : Schematic – Stepper motor driver

### 5.2.1.2. Control design

The remote control mainly consists of the following components:-

1. Microcontroller - For system control
2. Serial to USB module - For communication with PC
3. Motor driver section - For sending motor control signals to the 2 motor driver boards.

Schematic of the control board is shown below.

### 5.2.1.3. Microcontroller (MCU) selection

Microcontroller selection is done depending on following requirements:-

1. Motor driver GPIO pins | - 8 nos.
2. Programming port (SPI) | - 1 nos.
3. Serial communication (UART) | - 1 no.
4. Timer interrupts | - 1 no.

All these can be achieved using Atmel ATmega16 MCU. Hence it is selected.


Figure 19 : Schematic – Control board


Figure 20 : Schematic – Power supply

### 5.2.2. Firmware design

The firmware in the Atmega16 MCU is designed as shown in below state diagram. A timer

interrupt is configured to give timed clock pulses for the motor driver board. Interrupts are

also configured for serial communication.

The pulse target command is received in the serial Rx interrupt and is used in the main loop.


Figure 21 : Firmware design - State diagram

## 5.3. Software design

A windows application has been developed for the mount control. This application is the

master of the entire system. Below is the screen-shot of the same. The application has been

developed using MS Visual Studio 2010 software.


Figure 22 : Software - Windows application

User can control the mount using the arrow keys in the “Normal” section of the application.

In the “Scanner” section, the user can set the scan area as X degrees by Y degrees; select

either of the 4 quadrants and click on “Scan” button to start the scan. The window also

displays the feedback received from the mount such as the status of the mount – whether it is

on or off; mode set in the mount; speed etc. in the status bar at the bottom.

## 5.4. Communication design

A communication protocol was designed to enable error free and reliable communication between the application software and the mount. The protocol was built upon serial communication as a base protocol. Below is the table showing the frame format for the designed protocol. It shows the different types of information and commands exchanged between the application and the mount.


Table 6 : Communication protocol - Frame format

The protocol is designed to ensure that corrupted data is discarded. This is done by implementing a redundancy check in the form of checksum. The “checksum” byte in the frame format is the sum of all the bytes in that frame before it. When the frame is received at the other entity, a fresh checksum is calculated of the received bytes and he result is compared with the received “checksum” byte. If the results match, only then the data is processed, else the entire frame is discarded.

## 6. Testing and Results

## 6.1. Test observations

The requirement specifications which were set at the start of the project were tested to check if they were achieved. Below are results of the same.

Requirement | Observations | Remarks
Load | The telescope mounted on the mount is of 1.2Kg which the mount is able to control. | Ok
Performance | The mount is theoretically designed to achieve 0.1° angular resolution, however due to some mechanical inaccuracies in assembly the mount is only able to achieve 0.2° resolution. | Though the resolution specification was not met, it is still very good for the purpose of astronomical observation.
Power | The mount is able to perform perfectly on a 12V DC supply. | Ok
Dimensions | The mount fits well within the required dimensions. | Ok
Communication | The mount and the computer application communicate with each other using an error free protocol. | Ok
Functional | The mount is able to perform as expected in the two modes for which it was designed. | Ok

Table 7 : Test observations

## 6.2. Setup Photos

Below are some photos of the mount and the overall system.


Figure 23 : Photo - Setup under test


Figure 24 : Photo - Test measurements


Figure 25 : Photo - Horizontal drive assembly

Above photo shows the base of the mount which houses the horizontal drive assembly. The gears, coupling and motor can be seen. Also can be seen are the control board on the left, the communication connector with the blue cable, and the power supply board on the right with the black cable.

Figure 26 : Photo - Mount interfaced with application software

## 7. Conclusion

As per the initial requirement, a mount for guiding a telescope was successfully designed

and developed. It was able to bear the load of the telescope and maneuver it. The mount was

working as expected in both the functional modes – Normal and Scanner. The mount was

also sufficiently good in angular resolution. As a result it was able to position the telescope

very accurately as the user desired.

The entire system is a good example of a “Mechatronics” system as it incorporates

concepts from various engineering fields like mechanical, electronics, software and

communication. Various challenges were faced while working in each of these fields and also

during their integration and testing. Having an inter-disciplinary approach was the key for

successful execution and completion of the project.

## 8. References

[1] Jacek F. Gieras, “Permanent Magnet Motor Technology”, CRC Press 2009
[2] John Bird, Carl Ross, “Mechanical Engineering Principles”, Routledge 2002
[3] Hans J. Kärcher, Ulrich Weis, Oliver Dreyer, Paul Jeffers, Giovanni Bonomi, “The azimuth axes mechanisms for the ATST telescope mount assembly”, Proceedings of SPIE -The International Society for Optical Engineering, 2008
[4] M. Kurita, S. Sato, N. Noda, “Ultra-Lightweight Telescope Mount”, Publications of the Astronomical Society of the Pacific, 2009
[5] Douglas R. Neill, Ed Hileman, Jacques Sebag, William Gressler, Oliver Wiecha, Michael Warner, Bill Schoening, “Baseline design of the LSST telescope mount assembly”, Conference: SPIE Astronomical Telescopes + Instrumentation, 2012
[6] Ms.Neha R. Laddha, Prof. A. P. Thakare, "A Review on Serial Communication by UART", International Journal of Advanced Research in Computer Science and Software Engineering, Volume 3, Issue 1, January 2013
[7] Gregor V. Bochmann And Carl A. Sunshine, “Formal Methods in Communication Protocol Design”, IEEE transactions on communications, vol. com-28, no. 4, april 1980
[8] Padmanabhan. S., Chandrasekaran. M. and Srinivasa Raman. V., “Design Optimization of Worm Gear drive”, International Journal of Mining, Metallurgy & Mechanical Engineering (IJMMME) Volume 1, Issue 1 (2013) ISSN 2320–4060 (Online)
[9] http://www.celestron.com/support/knowledgebase
[10] http://www.skyatnightmagazine.com/

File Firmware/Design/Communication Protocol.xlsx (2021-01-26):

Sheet: Protocol_Comm
 |  |  |  |  |  |  | 0 | 1 | 2 | 3
Frame Type | Command | Direction | Mode | SOF | Frame# | DLC | Data (L = DLC, MSB 1st) |  |  |  | Check Sum | EOF
 |  |  |  |  |  |  | D3 | D2 | D1 | D0
Req01 | Start Stop | PC → Mount | - | 0x55 | 0x11 | 1 | - | - | - | 0 - Stop 1 - Start | 0xXX | 0x5A
Req02 | Speed | PC → Mount | - | 0x55 | 0x12 | 1 | - | - | - | Speed Divider | 0xXX | 0x5A
Req03 | Mode | PC → Mount | - | 0x55 | 0x13 | 1 | - | - | - | 0 - Normal 1 - Scan | 0xXX | 0x5A
Req04 | Direction | PC → Mount | Normal | 0x55 | 0x14 | 1 | - | - | - | B7-B4 : V Direction 0 - CW 1 - CCW B3-B0 : H Direction 0 - CW 1 - CCW | 0xXX | 0x5A
Req05 | Pulse Count | PC → Mount | Normal | 0x55 | 0x15 | 4 | Vertical pulse count (0 - 65536) (D3 - MSB ; D2 - LSB) |  | Horizontal pulse count (0 - 65536) (D1 - MSB ; D0 - LSB) |  | 0xXX | 0x5A
Req06 | Zero | PC → Mount | Scan | 0x55 | 0x16 | 1 | - | - | - | 0 - Normal 1 - Set Zero | 0xXX | 0x5A
Req07 | Quadrant | PC → Mount | Scan | 0x55 | 0x17 | 1 | - | - | - | 1 - 1st quad 2 - 2nd quad 3 - 3rd quad 4 - 4th quad | 0xXX | 0x5A
Req08 | Degrees | PC → Mount | Scan | 0x55 | 0x18 | 4 | Vertical degrees count (0 - 65536) (D3 - MSB ; D2 - LSB) |  | Horizontal degrees count (0 - 65536) (D1 - MSB ; D0 - LSB) |  | 0xXX | 0x5A
Res01 | System Status | Mount → PC | - | 0x55 | 0x21 | 4 | B7-B4 : V Direction 0 - CW 1 - CCW B3-B0 : H Direction 0 - CW 1 - CCW | Reserved 0x00 | Speed Divider | B0 : Sys Status 0 - Stop 1 - Start B1 : Mode 0 - Normal 1 - Scan | 0xXX | 0x5A
Res02 | Pulse Count | Mount → PC | Normal | 0x55 | 0x25 | 4 | Vertical pulse elapsed (0 - 65536) (D3 - MSB ; D2 - LSB) |  | Horizontal pulse elapsed (0 - 65536) (D1 - MSB ; D0 - LSB) |  | 0xXX | 0x5A
Res03 | Quadrant | Mount → PC | Scan | 0x55 | 0x27 | 1 | - | - | - | 1 - 1st quad 2 - 2nd quad 3 - 3rd quad 4 - 4th quad | 0xXX | 0x5A
Res04 | Degrees | Mount → PC | Scan | 0x55 | 0x28 | 4 | Vertical degrees elapsed (0 - 65536) (D3 - MSB ; D2 - LSB) |  | Horizontal degrees elapsed (0 - 65536) (D1 - MSB ; D0 - LSB) |  | 0xXX | 0x5A

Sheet: Pulse tests
 |  |  |  |  |  |  |  |  | speed = 3
 |  |  |  |  |  |  |  |  | step count | 3000 |  |  | 2000 |  |  | 1000 |  |  | 500 |  | 400 |  | 60 |  | 40 |  | 20
 | 1 pulse | 1 | step |  |  |  |  |  |  | ang 1 | ang 2 | diff | ang 1 | ang 2 | diff | ang 1 | ang 2 | diff | ang 1 | ang 2 | ang 1 | ang 2 | ang 1 | ang 2 | ang 1 | ang 2 | ang 1 | ang 2
 | 1 step | 1 | pulses |  |  |  |  |  | 1 | 2.5 | 28.5 | 26 | 71.3 | 51.2 | 20.1 | 72.2 | 82.4 | 10.2 |  |  |  |  | 64.9 |  | 65.6
 |  |  |  |  |  |  |  |  | 2 | 28.5 | 49.3 | 20.8 | 51.2 | 72.2 | 21 | 82.4 | 75.9 | 6.5 |  |  |  |  | 65.2 |  | 66.2
 | 1 step | 0.0225 | deg |  |  |  |  |  | 3 | 73.6 | 43.3 | 30.3 |  |  |  | 75.9 | 64.5 | 11.4 |  |  |  |  | 65.7 |  | 66.5
 |  |  |  |  |  |  |  |  | 4 | 43.3 | 75 | 31.7 |  |  |  |  |  |  |  |  |  |  | 66.2 |  | 66.8
 | 1 deg | 44.44444444 | steps |  |  |  |  |  | 5 | 75 | 43.7 | 31.3 |  |  |  |  |  |  |  |  |  |  | 66.8 |  | 67.2
 |  | 44.44444444 | pulses |  |  |  |  |  |  | 43.7 | 12 | 31.7 |  |  |  |  |  |  |  |  |  |  | 67.3 |  | 67.5
 |  | 44 |  |  |  |  |  |  |  |  |  |  |  |  |  |  |  |  |  |  |  |  |  |  | 68.1
 |  |  |  |  |  |  |  |  |  |  |  |  |  |  |  |  |  |  |  |  |  |  |  |  | 67.9
degrees | 15 | 30 | 45 | 60 | 90 | 120 | 150 | 180 |  |  |  |  |  |  |  |  |  |  |  |  |  |  | -0.3 |  | 67.7
pulses | 660 | 1320 | 1980 | 2640 | 3960 | 5280 | 6600 | 7920 |  |  |  | 28.63333333 |  |  |  |  |  | 9.366666667 |  |  |  |  | -0.5 |  | 67.4
 |  |  |  |  |  |  |  |  |  |  |  |  |  |  |  |  |  |  |  |  |  |  | -0.5
 |  |  |  |  |  |  |  |  |  |  |  |  |  |  |  |  |  |  |  |  |  |  | -0.6
 |  |  |  |  |  |  |  |  |  |  |  |  |  |  |  |  |  |  |  |  |  |  | -0.5
 |  |  |  |  |  |  |  |  |  |  |  |  |  |  |  |  |  |  |  |  |  |  |  |  | -0.6
 |  |  |  |  |  |  |  |  |  |  |  |  |  |  |  |  |  |  |  |  |  |  |  |  | -0.3
 |  |  |  |  |  |  |  |  |  |  |  |  |  |  |  |  |  |  |  |  |  |  |  |  | -0.3
 |  |  |  |  |  |  |  |  |  |  |  |  |  |  |  |  |  |  |  |  |  |  |  |  | -0.4
 |  |  |  |  |  |  |  |  |  |  |  |  |  |  |  |  |  |  |  |  |  |  | -0.48 |  | -0.3
 |  |  |  |  |  |  |  |  |  |  |  |  |  |  |  |  |  |  |  |  |  |  |  |  | 0.2
 |  |  |  |  |  |  |  |  |  |  |  |  |  |  |  |  |  |  |  |  |  |  |  |  | 0.2
 |  |  |  |  |  |  |  |  |  |  |  |  |  |  |  |  |  |  |  |  |  |  |  |  | 0.3
 |  |  |  |  |  |  |  |  |  |  |  |  |  |  |  |  |  |  |  |  |  |  |  |  | -0.15

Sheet: Quad_Dir
 | U
L | D | R
 | CW |  | h | v | h |  |  | h | v | h
CCW | CCW | CW | CCW | CW | CW |  |  | CW | CW | CCW
 |  |  |  |  |  | 2 | 1
 |  |  |  |  |  | 3 | 4
 |  |  | h | v | h |  |  | h | v | h
 |  |  | CCW | CCW | CW |  |  | CW | CCW | CCW
 |  |  |  |  |  |  | Q | h | v | h
 |  |  |  |  |  |  | 1 | CW | CW | CCW
 |  |  |  |  |  |  | 2 | CCW | CW | CW
 |  |  |  |  |  |  | 3 | CCW | CCW | CW
 |  |  |  |  |  |  | 4 | CW | CCW | CCW

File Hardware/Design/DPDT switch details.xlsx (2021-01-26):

pin # |  |  |  |  |  | pin # |  |  |  |  |  |  | 8mm
1 | NO2 | a | p | C1 |  | 5 | pr | NO | not pressed
3 | NC2 | b | q | NC1 |  | 6 | pq | NC | pressed |  |  |  | 6.16mm out
2 | C2 | c | r | NO1 |  | 4 | cb | NC | pressed |  |  | 1 |  |  | 5
 |  |  |  |  |  |  | ca | NO | not pressed | 2.08mm in |  |  |  | V
 |  |  |  |  |  |  |  |  |  |  |  | 3 |  |  | 6 | 8mm
 |  |  |  |  | NO1 |  |  |  |  |  |  | 2 |  | H | 4
C1
 |  |  |  |  | NC1
C2 |  |  |  |  | NO2
 |  |  |  |  |  |  |  |  |  |  | 0.6mm
 |  |  |  |  | NC2
 |  |  |  |  |  |  |  |  |  |  |  | 0.22mm
 |  |  |  |  |  |  |  |  | 0.106 | V c/c dist | 2.68
 |  |  |  |  |  |  |  |  | 0.209 | H c/c dist | 5.3

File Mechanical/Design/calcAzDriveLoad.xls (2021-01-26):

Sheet: Azimuth_Motion
Load calculations for "Azimuth motion"
Item | Value | Unit | Description | Telescope + mount load
qload | 0.1 | degree | Req angular displacement resolution | Item | Value | Unit | Description
tload | 22.50 | kg-cm | Required load | Wt | 2 | Kg | Total weight of scope and mount with altitude mechanism
 |  |  |  | Len | 12 | inches | end to end max. length of above mechanism.
a | 40 |  | Gear ratio |  | 30 | cm
 |  |  |  | FOS | 1.5 |  | factor of safety
qm | 1.8 | degree | Req motor step angle
tm | 0.56 | kg-cm | Req motor torque | tload = Wt/2 x FOS x Len/2 |  |  | Formula for Torque
 |  |  |  | tload | 22.50 | Kg-cm
Note -
 | Input values in green cells
 | Output values in yellow cells

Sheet: Gear_Detailed_Calc
Angular displacement Calculations
 | Item | Value | Unit | Description
 | TG | 40 |  | No. of teeth on gear "G"
 | TW | 1 |  | No. of teeth/helix on worm "W"
 | a | 40 |  | gear ratio
 | q1 | 1.8 | degree | Step angle of motor (assume)
 | qfull | 360 | degree
 |  | 200 |  | No of motor steps per revolution of worm
 |  | 200 |  | No of motor steps for displacing 1 tooth of Gear "G"
 | Tx | 0.005 |  | No of tooth of "G" displaced in 1 motor step
 | q2 | 9 | degree | Angle displcement by displacing 1 tooth of "G"
 | qload | 0.045 | degree | Therefore, angle displcement by displacing Tx tooth of "G". Which is nothing but angle displaced of gear wheel "G" for 1 motor step.
 | qload req | 0.1 | degree | Required angluar resolution
 | Result | OK |  | OK - ok and valid design ; NG - not good. Please re-enter input values (green)

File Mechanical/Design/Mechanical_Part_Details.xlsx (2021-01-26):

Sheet: Part_Tree
Part Tree |  |  |  |  |  | Part list | Design Status | Design Remarks | Manufacturing status | Manufacturing Remarks
Level 1 | Level 2 | Level 3 | Level 4 | Level 5 | Level 6
Mount | Base | Frame | Base plate |  |  | Base plate | Done |  | Done
 |  |  | Wall |  |  | Wall | Done |  | To be started | Spacer studs to be used
 |  |  | Top plate |  |  | Top plate | Done |  | Done
 |  | Horizontal Drive | Motor |  |  | Motor | Done |  | NA
 |  |  | Motor frame H | Base |  | Motor frame H Base | Done |  | Done
 |  |  |  | Face |  | Motor frame H Face | Done |  | Done
 |  |  | Coupling |  |  | Coupling | Done |  | NA
 |  |  | Gear Set 1 | Worm 1 |  | Worm 1 | Done |  | Done
 |  |  |  | Wheel 1 |  | Wheel 1 | Done |  | Done
 |  |  | Bearing Set 1 | Worm 1 bearing |  | Worm 1 bearing | Done |  | NA
 |  |  |  | Wheel 1 bearing |  | Wheel 1 bearing | Done |  | NA
 |  |  |  | Bearing housing 1 | Base | Bearing housing 1 Base | Done |  | Done
 |  |  |  |  | Side | Bearing housing 1 Side | Done |  | Done
 |  |  |  |  | Top | Bearing housing 1 Top | Done |  | Done
 | Turn table | Frame | Base plate |  |  | Base plate | Done |  | To be started
 |  |  | Vertical frame |  |  | Vertical frame | WIP | check height of scope with star diagonal focussed | To be started
 |  | Vertical Drive | Motor |  |  | Motor | Done |  | Done
 |  |  | Motor frame V | Top |  | Motor frame V Top | Done |  | Done
 |  |  |  | Wall |  | Motor frame V Wall | Done |  | Done
 |  |  | Coupling |  |  | Coupling | Done |  | NA
 |  |  | Gear Set 2 | Worm 2 |  | Worm 2 | Done |  | Done
 |  |  |  | Wheel 2 |  | Wheel 2 | Done |  | Done
 |  |  | Bearing Set 2 | Worm 2 bearing |  | Worm 2 bearing | Done |  | NA
 |  |  |  | Wheel 2 bearing |  | Wheel 2 bearing | Done |  | NA
 |  |  |  | Bearing housing 2 | Base | Bearing housing 2 Base | Done | same as BH1 | Done
 |  |  |  |  | Side | Bearing housing 2 Side | Done | same as BH1 | Done
 |  |  |  |  | Top | Bearing housing 2 Top | Done | same as BH1 | Done
 |  | Support Column | Vertical frame |  |  | Vertical frame | Done |  | To be started
 |  |  | Shaft |  |  | Shaft | WIP | exact dimensions TBD | To be started
 |  |  | Housing/ Spacer |  |  | Housing/ Spacer | WIP |  | To be started
 | Scope attachment |  |  |  |  | Scope attachment | To be started |  | To be started

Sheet: ToDo
1 | confirm gear PCD!!

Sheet: Conversion
Inches --> | mm
0.187 | 4.582
mm --> | Inches
5 | 0.204

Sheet: Gear_Details
 |  |  |  |  |  |  |  | Wheel shaft |  |  |  |  |  |  | Wheel shaft
 |  |  |  |  |  |  |  | OD at wheel |  | 13 |  |  |  |  | OD at wheel |  | 15
 |  |  |  |  | Worm Wheel |  |  | OD at bearing |  | 12 |  | Worm Wheel |  |  | OD at bearing |  | 12 |  | Worm Wheel
 |  |  |  |  | OD 43 x 15 thick |  |  |  |  |  |  | OD 43 x 15 thick |  |  |  |  |  |  | OD 43 x 15 thick
 |  |  |  |  | 1 Module x 40 Teeth |  |  |  |  |  |  | 1 Module x 40 Teeth |  |  |  |  |  |  | 1 Module x 40 Teeth
 |  |  |  |  | PB2 |  |  |  |  |  |  | PB2 |  |  |  |  |  |  | PB2
 |  |  |  |  |  |  | 28 | 25 | 28 |  |  | PCD | 41 | 20 | 59 | 20 |  |  | PCD | 41
 |  |  |  |  |  |  |  |  |  |  |  | ID | 13 |  |  |  |  |  | ID | 15
 |  |  |  |  |  |  |  |  |  |  |  | t | 15 |  |  |  |  |  | t | 19
 |  |  |  |  |  |  |  | 12 |  |  |  |  | M | 12 |  |  |  |  |  | M
 |  |  |  |  |  |  |  |  | 15 | 42 | 25 |  |  |  | 18 |  | 23 | x
 |  |  |  |  |  |  |  |  |  | + 2 mm on each side |  |  |  |  |  |  | + 2 mm on each side
 |  |  |  | Worm |  |  |  |  |  | =46 | Worm |  |  |  |  |  |  | Worm
 |  |  |  | 1 start, OD 20 |  |  |  |  |  |  | 1 start, OD 20 |  |  |  |  |  |  | 1 start, OD 20
 |  |  |  | EN8/C45 |  |  |  |  |  |  | EN8/C45 |  |  |  |  |  |  | EN8/C45
 |  |  |  |  |  |  |  |  |  |  | PCD | 18 |  |  |  |  |  | PCD | 18
 |  |  |  |  |  |  |  |  |  |  | shaft dia | 12 |  |  |  |  |  | shaft dia | 12
 |  | Given Data by Precision gears |  |  |  |  |  |  |  | Gear Set 1 |  |  |  |  |  |  | Gear Set 2
 |  |  |  |  |  |  |  |  |  | Horizontal |  |  |  |  |  |  | Vertical
All dim in mm.
 |  |  | PCD | R | R - 1 mm | ?? Why mod = 1?? |  |  | actual | set 1 |  |  |  |  |  | actual | set 2
Wheel | OD | 43 | 41 | 21.5 | 20.5
Worm | OD | 20 | 18 | 10 | 9 |  |  |  |  |  |  |  |  |  | 15
 |  |  |  |  |  |  |  | 13
 |  |  |  | c/c distance | 29.5 |  |  |  | 50 | 40 | 86 (62 usable) |  |  |  | 18 |  | 24 | 148

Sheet: Motor_Details
A | 47
B | 42
L | 47 | inner | Motor frame H
H | 42 | inner
h | 21
Wf | 72
Wb | 42 | step down at half len
 |  |  |  |  | h |  | H
 |  |  |  |  |  | Wb
 |  |  |  |  |  |  |  | L
 |  |  |  | Wf

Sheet: Coupling
Part no | AF 25-6-10
L | 32 | mm
depth of (d2) | 22 | mm
depth of (d1) | 10 | mm
Qty | 2 | nos
Latest CAD file |  | Coupling_V2.0

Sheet: Bearing
Part no | 6800Z
ID | 10 | mm
OD | 19 | mm
Th | 5 | mm
Qty | 10 | nos
Latest CAD file |  | Bearing_V2.0

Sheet: Bearing_Housing
 |  |  |  |  | Thick | 5.6
 |  | l |  |  | Bearing Housing 1 - Horizontal - v0.1 |  |  |  | Bearing Housing 1 - Horizontal - v0.6
 |  |  |  |  | Parameter |  | L |  | Parameter | L | W | H | l | w | h | a | φ D1 | φ D2
 |  |  |  |  | Main Dependency |  | Worm L & Wheel D |  | Main Dependency | Worm L & Wheel D | Wheel + Worm D | Worm D & Motor CL | Wheel R | Wheel R | Worm R & Motor CL | Worm R | Wheel S D | Worm S D
 |  |  |  |  | Actual (GS1) |  | 43 |  | Actual (GS1) | 43 | 63 | 42 | 21.5 | 21.5 | 21 | 10 | 12 | 12
 |  |  |  | H | Gap(each side) |  | 3 |  | Gap(each side) | 3 | 3 | 0 | 3 | 3 | 0 | 2 | 8 | 8
 |  |  |  |  | Act + Gap |  | 49 |  | Act + Gap | 49 | 69 | 42 | 24.5 | 24.5 | 21 | 15 | 28 | 28
 |  |  |  |  | Outer |  | 60.2 |  | Outer | 60.2 | 80.2 | 53.2 | - | - | - | - | - | -
 |  |  |  |  |  |  |  |  |  |  | 69 | 26.6 |  | 24.5 |  | 15 |  | 29.5
 |  |  | h |  |  |  |  | 0 |  |  |  |  |  |  |  |  |  | 29.5 | 0
 |  |  |  |  | Bearing Housing 2 - Vertical
a |  |  |  |  | Parameter |  | L
 |  |  |  |  | Main Dependency |  | Worm D
 |  |  |  | w
 |  |  |  |  | Value 1
 |  |  |  | W | Value 2
 |  |  |  |  | Value 3
 | L |  |  |  | Value 4
 |  |  |  | All dimensions in mm | "D" means gear shaft φ including it's bearing φ (OD)

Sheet: BH1_v0.6
check for V0.6
 | 14.367 |  | 14.367 |  | 12.033 |  | 12.033
 | 5.6 |  | 5.6 |  | 5.6 |  | 5.6
YZ - Y | 19.967 | 20.267 | 19.967 | YZ - Z | 17.633 | 17.933 | 17.633 | XY - X | 26.833 | 26.533 | 26.833
 |  |  |  |  | 12.233 |  | 12.233
 |  |  |  |  | 5.6 |  | 5.6
XY - Y | 20.167 | 19.867 | 20.167 | XZ - Z | 17.833 | 17.533 | 17.833 | XZ - X | 26.633 | 26.933 | 26.633
delta | -0.2 | 0.4 | -0.2 |  | -0.2 | 0.4 | -0.2 |  | 0.2 | -0.4 | 0.2

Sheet: Base_plate
Base plate dimensions
Ro | 150
Rh | 7
Rp | 145
Bl | ref
Bw | ref
Pwi | 15
Pwo | 25
Pho | 70 | tbd
Pt | 6
Pcw | 5
Boh | TBD
Bov | TBD

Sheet: observation
 | 20141129 observation
 | Part - BH1_YZ_v0.4 |  |  | observed delta | 0.2
fresh | given dim | observed dim | delta |  |  | tol = .4 |  | tol = .3 |  | tol = .2 |  | tol = .1
male | 14.677 | 14.500 | 0.177 | 14.767 | 14.567 | 11.4 | 11.2 | 11.4 | 11.2 | 11.4 | 11.2 | 11.4 | 11.2
female | 18.647 | 18.860 | -0.213 | 18.46 | 18.66 | 11 | 11.2 | 11.1 | 11.3 | 11.2 | 11.4 | 11.3 | 11.5
 |  |  |  |  | forced delta | 0.4 |  | 0.3 |  | 0.2 |  | 0.1
 |  |  |  |  | predicted manufactuirngdelta |  | 0 |  | -0.1 |  | -0.2 |  | -0.3
cold |  |  |  |  |  | fitting :- |  |  |  | fitting :-
male | 11.400 | 10.800 | 0.600 |  |  | fits when fresh. |  |  |  | ok desu!
female | 11.000 | 11.400 | -0.400 |  |  | not fitting 30 mins later

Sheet: Sheet1
 |  | GS2 worm |  | GS2 wheel
 | inner | 49 | inner | 42
 | thick | 5.6 | thick | 5.6
 | thick | 5.6 | thick | 5.6
 | gap to cplng | 5 | gap to dovetail | 10 | x
 | depth in cplg | 12 | depth in dovetail | 10 | y
 | back shaft | 3 | back shaft | 3
 | worm L | 80.2 | wheel shaft L | 76.2
 | cut LHS L | 18 |  | OK
 | worm cut L | 24
5 | cut RHS L | 38.2
12
5.6
22.6 | max L | 148
15.6 | avl for wheel | 109.8

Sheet: ScopeHolder
80.2 | mm
 |  | 32 | mm
 |  |  |  | total L | 260 | mm
 |  | 9 | inch
 |  | 228 | mm


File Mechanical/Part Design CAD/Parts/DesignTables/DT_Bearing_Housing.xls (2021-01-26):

PartNo | L (mm) | W (mm) | H (mm) | l (mm) | w (mm) | h (mm) | a (mm) | D1 (mm) | D2 (mm) | Thick (mm)
BH1_act | 49 | 69 | 26 | 24.5 | 24.5 | 13 | 13 | 12 | 12 | 6

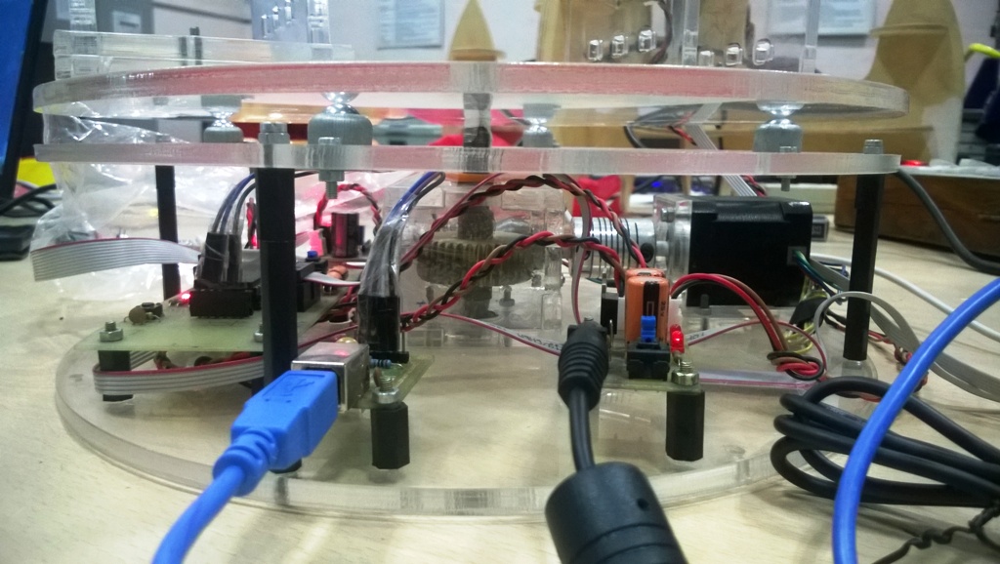
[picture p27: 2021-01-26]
Mechanical/Photos/H_04.jpg

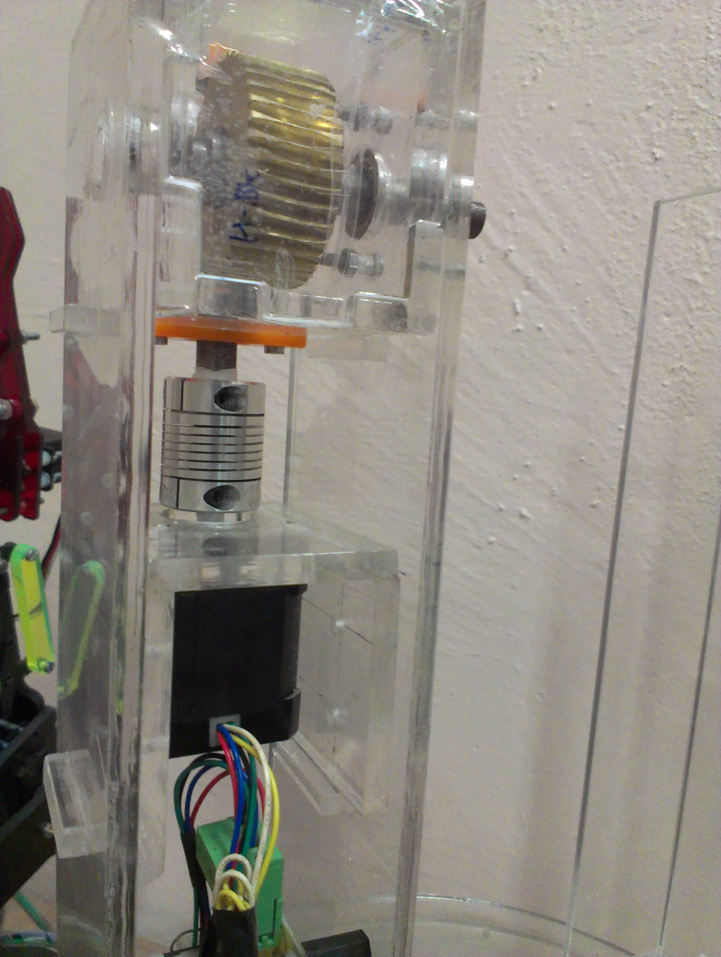
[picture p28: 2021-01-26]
Mechanical/Photos/V_03.jpg

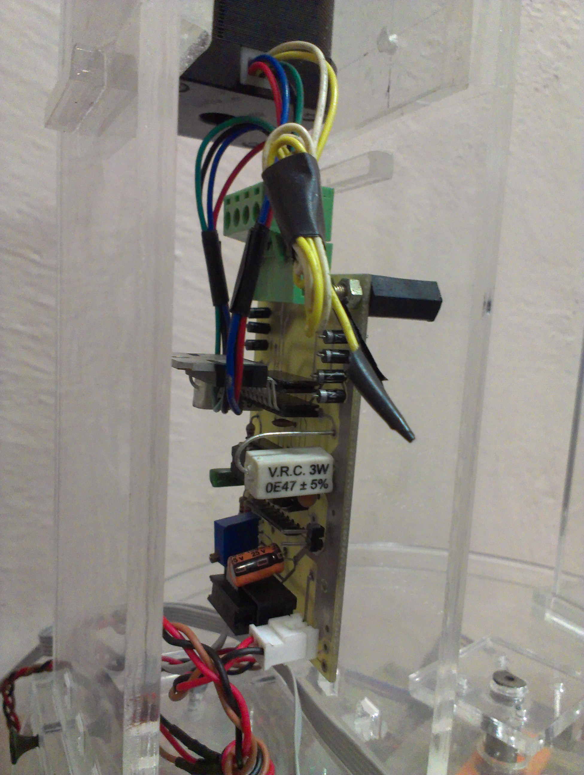
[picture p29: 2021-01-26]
Mechanical/Photos/V_04.jpg

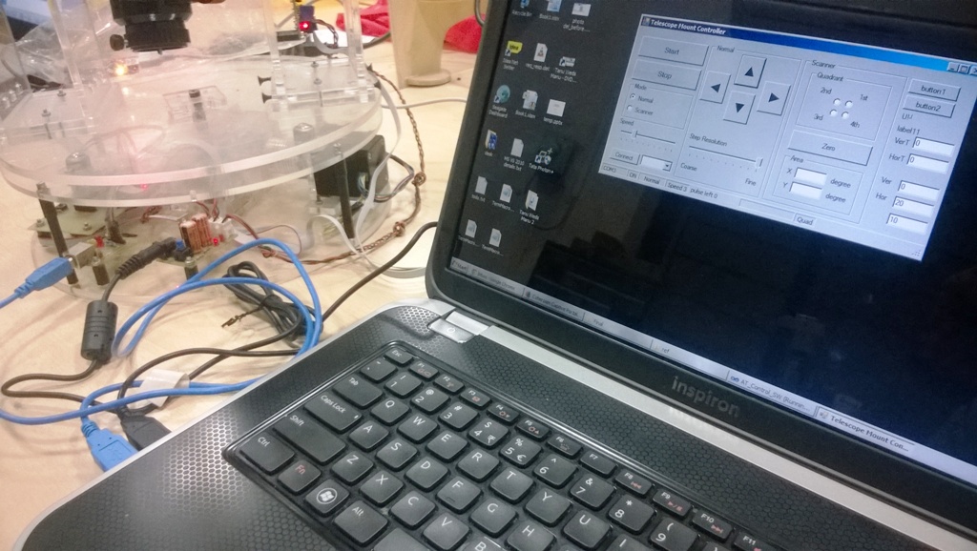
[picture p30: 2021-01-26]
Mechanical/Photos/1_PC_app.jpg

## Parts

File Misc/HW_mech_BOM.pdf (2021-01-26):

Sr No | Component | Details/ Specification | Quantity | Remarks | Reference
1 | Stepper motor

Step Angle : 0.9degree
Part no - 4209L - 03 - 01

2

exactly the same one which we have in COEP fab lab. Black colour motor

2 | Micro controller | Atmega16A | 1 | 40 pin DIP package
3 | IC base | 40 pin DIP IC base | 1 | for mounting microcontroller on PCB | -
4 | Micro controller programmer | AVR usb programmer | 1

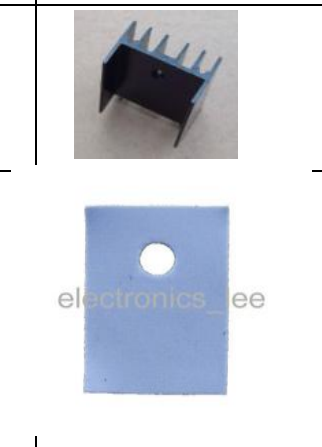
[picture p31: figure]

5 | IC L298 | 15 pin IC. Vertical pacakage | 1
6 | Heat sink for L298 | | 2

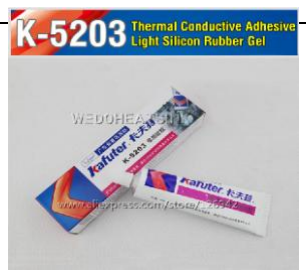
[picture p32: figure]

7 | Silica rubber and gel | needed for good conduction of heat sink | 2
8 | IC OP07 | OP AMP IC 8pin DIP package | 5 | if OP07 not available, IC 741 is also ok

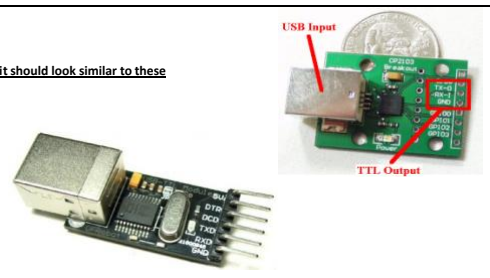
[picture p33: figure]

9 | USB-to-TTL module | not USB-to-RS232 | 1 | output should be TTL only, which can directly be given to microcontroller. RS232 output is not useful. Should NOT have DB9 connector | it should look similar to these
10 | USB cable | | 1 | for connecting PC USB port to above module and AVR programmer. A and B type connectors
11 | Resistors | 4.7k, 1/4 watt | 10
| | 10k blue colour single turn trim pot | 1
| | 0.1 ohm 3 Watt | 6
| | 9 pin resistor bank - 10k ohm | 4
12 | LED | red colour SMD 1206 package | 10 | SMD package only

## 1. Electronic Components

13 | Diode | FAIRCHILD SEMICONDUCTOR - S2M -DIODE | 20 | SMD package only

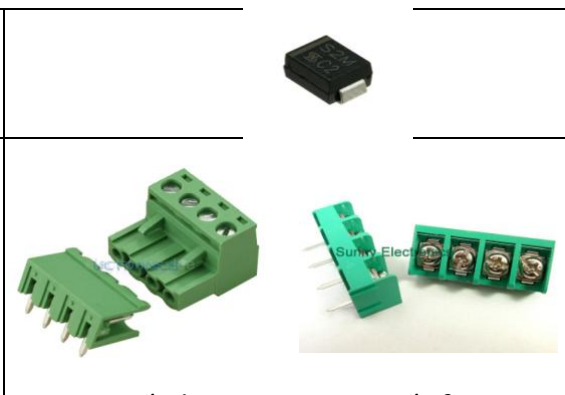
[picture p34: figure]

14 | 4 pin plug-in screw connector (for motor) | male female pair | 2 | option 1 preffered. If not available, then option 2 also ok. | option 1 option 2
15 | 3 Amp wire (for motor) | | 1.5 meter
16 | Multi strand wire | red colour | 0.5 meter
17 | | black colour | 0.5 meter
18 | 12V adaptor | male female pair | 2
19 | Buttons | push button (momentary) | 10 | need to press/hold continously to turn ON. If SMD package available, it will be preferred
| | push button (detent type) | 3 | need to press only once to turn ON/OFF If SMD package available, it will be preferred
20 | Crystal | Flat type 12Mhz | 1
21 | 2 pin connector (relimate) | male female pair. Male part for PCB mounting. Female part with wire | 3 | if 2 pin not available, 4 pin also ok

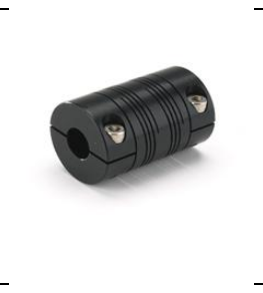
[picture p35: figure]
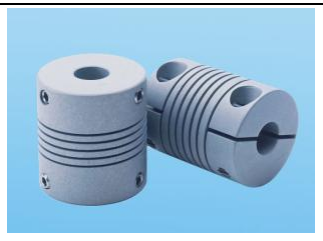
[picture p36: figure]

Part numbers listed here -

Make - Rocomcorp :-

ATOOM075-C10MM-C5MM

ATOOM075-C.375-C.187

Make - Encoders India :-

AHC 25-32-5x10

23 Ball Bearing

Part no-6800ZZ
61900

10

Specification-ID = 10mm
OD < 25mm (the smaller the better) Thickness = 5 or 6mm (not more)
- Please try to get any 1 of the part number
mentioned starting from top.
- If exact part number not available, get the one which fits above specification.
Total Qty 10

Encoder Coupling.
Specification -
ID1 = 5mm
ID2 = 10mm
OD < 28mm (the smaller the better). Length < 30mm (the smaller the better).
- Please try to get any 1 of the part number
mentioned starting from top.
- If exact part number not available, get the one which fits above specification.
Total Qty 3
22 | Coupling | 3

## 2. Mechanical Components

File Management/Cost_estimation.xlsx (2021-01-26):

Astro Tracker Project | Sanket Garade | Rough Estimate
Sr. No. | Item | Qty | Rate | Amount (Rs.) | Remarks
A | Mechanical
1 | Equatorial Mount | 1 | 5000 | 5000
2 | Telescope OTA | 1 | 6000 | 6000 | Mount + telescope + tripod can be bought in 1 single package.
3 | Tripod | 1 | 3000 | 3000
4 | Gears/ gearbox | 1 | 2000 | 2000 | Rough estimate. Will purchase gears according to design.
5 | Enclosure for gear and motor assembly | 1 | 2000 | 2000 | Rough estimate. Will manufacture enclosure by preparing CAD file of same.
6 | Misc (couplings, fasteners, nut-bolts etc.) | 1 | 2000 | 2000 | Rough estimate.
 |  |  |  | 0
 | Total (Mechanical) |  |  | ₹20000
B | Electronics
1 | Stepper Motor | 3 | 300 | 900 | 2 needed (+ 1 for backup)
2 | Microcontroller | 2 | 200 | 400 | Planning to use either a PIC, AVR or TI's TMS320F28030 Picollo.
3 | Microcontroller debugger | 1 | 500 | 500
4 | Stepper motor controller IC L297 | 4 | 100 | 400 | 2 needed (+ 2 for backup)
5 | Motor driver IC L298 | 4 | 150 | 600 | 2 needed (+ 2 for backup)
6 | Active and Passive components (R,L,C,D,Q) | 50 | 5 | 250
7 | USB to serial (TTL) convertor module | 1 | 500 | 500
8 | USB cable | 1 | 100 | 100
9 | Misc (bread board, wires, op-amp etc.) | 1 | 300 | 300
10 | Tools (cutter, stripper, soldering gun etc.) | 1 | 700 | 700
 |  |  |  | 0
 | Total (Electronics) |  |  | ₹4650
C | Software
1 | MCU development IDE | 1 | 0 | 0 | Code limited trial version can be used which is free.
2 | Stellarium | 1 | 0 | 0 | Free software
3 | MS Visual Studio | 1 | 0 | 0 | Pre installed on most TCS PCs.
 | Total (Software) |  |  | 0
 | Total Amount (A+B+C) |  |  | ₹24650 | This estimate is rough and may fluctuate ± Rs 3000

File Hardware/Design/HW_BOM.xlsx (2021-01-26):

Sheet: All Parts
Board | Part Ref | Value | Qty | Procured? | Remarks
PS | C1 | 100u | 1 | No
PS | C2 | 100u | 1 | No
PS | C3 | 100n | 1 | Yes
PS | C4 | 100n | 1 | Yes
PS | CN1 | 3 pin | 1 | Yes
PS | CN2 | 3 pin | 1 | No
PS | CN3 | 3 pin | 1 | No
PS | CN4 | 3 pin | 1 | No
PS | D1 | Red LED | 1 | Yes
PS | D2 | Red LED | 1 | Yes
PS | R1 | 1.1k | 1 | Yes
PS | R2 | 470 | 1 | Yes
PS | SW1 | DPDT | 1 | Yes
PS | TP1 | NA | 1 | Yes
PS | TP2 | NA | 1 | Yes
PS | TP3 | NA | 1 | Yes
PS | TP4 | NA | 1 | Yes
PS | U1 | LM7805 | 1 | Yes
Control | C1 | 100u | 1 | Yes
Control | C2 | 100u | 1 | Yes
Control | C3 | 100n | 1 | Yes
Control | C4 | 100n | 1 | Yes
Control | C5 | 100n | 1 | Yes
Control | C6 | 100n | 1 | Yes
Control | CN1 | 3 pin | 1 | No
Control | CN2 | FRC 10 pin | 1 | No
Control | CN3 | Serial Comm | 1 | Yes
Control | CN4 | FRC 10 pin | 1 | No
Control | D1 | Red LED SMD | 1 | Yes
Control | D2 | Red LED SMD | 1 | Yes
Control | D3 | Red LED SMD | 1 | Yes
Control | D4 | Red LED SMD | 1 | Yes
Control | D5 | Red LED SMD | 1 | Yes
Control | D6 | Red LED SMD | 1 | Yes
Control | D7 | Red LED SMD | 1 | Yes
Control | D8 | Red LED SMD | 1 | Yes
Control | D9 | Red LED SMD | 1 | Yes
Control | D10 | Red LED SMD | 1 | Yes
Control | D11 | Red LED SMD | 1 | Yes
Control | D12 | Red LED SMD | 1 | Yes
Control | D13 | Red LED SMD | 1 | Yes
Control | JP1 | 2 pin JP | 1 | Yes
Control | JP2 | 2 pin JP | 1 | Yes
Control | JP3 | 2 pin JP | 1 | Yes
Control | JP4 | 2 pin JP | 1 | Yes
Control | JP5 | 2 pin JP | 1 | Yes
Control | R1 | 10k | 1 | Yes
Control | R2 | 1.1k | 1 | Yes
Control | R3 | 470 | 1 | Yes
Control | R4 | 470 | 1 | Yes
Control | R5 | 470 | 1 | Yes
Control | R6 | 470 | 1 | Yes
Control | R7 | 1.1k R bank 10 pin | 1 | No
Control | SW1 | DPDT | 1 | Yes
Control | SW2 | Up | 1 | Yes
Control | SW3 | Down | 1 | Yes
Control | SW4 | Left | 1 | Yes
Control | SW5 | Right | 1 | Yes
Control | SW6 | Zero | 1 | Yes
Control | SW7 | Speed | 1 | Yes
Control | SW8 | TBD1 | 1 | Yes
Control | SW9 | TBD2 | 1 | Yes
Control | SW10 | Reset | 1 | Yes
Control | TP1 | NA | 1 | Yes
Control | TP2 | NA | 1 | Yes
Control | TP3 | NA | 1 | Yes
Control | TP4 | NA | 1 | Yes
Control | TP5 | NA | 1 | Yes
Control | TP6 | NA | 1 | Yes
Control | TP7 | NA | 1 | Yes
Control | TP8 | NA | 1 | Yes
Control | TP9 | NA | 1 | Yes
Control | TP14 | NA | 1 | Yes
Control | TP15 | NA | 1 | Yes
Control | TP16 | NA | 1 | Yes
Control | U1 | LM7805 | 1 | Yes
Control | U2 | ATMEGA16L | 1 | Yes
Driver | C1 | 100u | 2 | No
Driver | C2 | 100u | 2 | No
Driver | C3 | 100n | 2 | No
Driver | C4 | 3n3 | 2 | No
Driver | C5 | 100n | 2 | No
Driver | C6 | 100n | 2 | No
Driver | CN2 | FRC 10 pin | 2 | No
Driver | CN3 | Screw in 4 pin | 2 | Yes
Driver | CN4 | 3 pin | 2 | No
Driver | D1 | 1N4001 | 2 | No
Driver | D2 | 1N4001 | 2 | No
Driver | D3 | 1N4001 | 2 | No
Driver | D4 | 1N4001 | 2 | No
Driver | D5 | 1N4001 | 2 | No
Driver | D6 | 1N4001 | 2 | No
Driver | D7 | 1N4001 | 2 | No
Driver | D8 | 1N4001 | 2 | No
Driver | D9 | Red LED | 2 | Yes
Driver | D10 | Red LED | 2 | Yes
Driver | JP1 | 2 pin JP | 2 | No
Driver | R1 | 10k | 2 | Yes
Driver | R2 | 10k | 2 | No
Driver | R3 | 22k | 2 | No
Driver | R4 | 0E47 3W | 2 | No
Driver | R5 | 0E47 3W | 2 | No
Driver | R6 | 1.1k | 2 | Yes
Driver | R7 | 470 | 2 | Yes
Driver | TP2 | NA | 2 | Yes
Driver | TP3 | NA | 2 | Yes
Driver | TP4 | NA | 2 | Yes
Driver | TP5 | NA | 2 | Yes
Driver | TP6 | NA | 2 | Yes
Driver | TP7 | NA | 2 | Yes
Driver | TP8 | NA | 2 | Yes
Driver | TP9 | NA | 2 | Yes
Driver | TP10 | NA | 2 | Yes
Driver | TP11 | NA | 2 | Yes
Driver | TP12 | NA | 2 | Yes
Driver | TP13 | NA | 2 | Yes
Driver | U1 | L297 | 2 | No
Driver | U2 | L298 | 2 | Yes
Misc | FRC cable | 10 pin | 1.5m | No
Misc | FRC connector | female | 6 | No
Misc | Red wire | 2 Amp | 1.5m | No
Misc | Black wire | 2 Amp | 1.5m | No
Misc | Silica rubber | 15cm x 15cm | <- | No
Misc | Sleeves | for wire | 15 cm | No
Misc | Sleeves | for shaft (6mm) | 15 cm | No
Misc | Castor wheel | AsmAP | 5 | No
Misc | Burg strip | female | 1 | No
Misc | Spacer studs | for board (AsAP) | 12 | No
Misc | Spacer studs | for mount (53.5mm) | 10 | No
Misc | IC base | 20 pin | 3 | No

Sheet: ToBeProcured
2015 01 10
Part Ref | Value | Qty
Cap | 1000u | 4
Cap | 470u | 2
Cap | 100n | 4
Cap | 3n3 | 4
Connector | FRC 10 pin PCB male | 4
Connector | 3 pin | 8
Diode | 1N4001 | 16
Jumper | 2 pin JP | 2
Res | 1k R bank 10 pin | 1
Res | 10k | 2
Res | 22k | 2
Res | 0E47 3W | 5
IC | L297 | 2
FRC cable | 10 pin | 1.5m
FRC connector | female | 6
Red wire | 2 Amp | 2m
Black wire | 2 Amp | 2m
Silica rubber | 15cm x 15cm | <-
Sleeves | for wire | 15 cm
Sleeves | for shaft (6mm dia) | 15 cm
Castor wheel | AsAP | 5
Burg strip | female | 1
Spacer studs | for board (AsAP) | 12
Spacer studs | for mount (53.5mm) | 10
IC base | 20 pin | 3

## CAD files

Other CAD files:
Mechanical/Part Design CAD/Assembly/Assembly_HDrive_v0.1.CATProduct
Mechanical/Part Design CAD/Assembly/BH1_trial.CATProduct
Mechanical/Part Design CAD/Assembly/BH1_v0.1.CATProduct
Mechanical/Part Design CAD/Assembly/BaseDriveH_Assembly_V0.1.CATProduct
Mechanical/Part Design CAD/Assembly/BaseFrame_Assembly_V0.1.CATProduct
Mechanical/Part Design CAD/Assembly/DriveH_Assembly_V1.0.CATProduct
Mechanical/Part Design CAD/Assembly/M_C_GS1_Constrained.CATProduct
Mechanical/Part Design CAD/Assembly/MotorFrameH_V0.1.CATProduct
Mechanical/Part Design CAD/Assembly/ScopeAssembly_V1.CATProduct
Mechanical/Part Design CAD/Board Base/BoardSetupBase.CATPart
Mechanical/Part Design CAD/Board Base/ControlBoard.CATPart
Mechanical/Part Design CAD/Parts/BF_Plate_V0.1.CATPart
Mechanical/Part Design CAD/Parts/BF_Wall_V0.1.CATPart
Mechanical/Part Design CAD/Parts/BH1_XY_Large_v0.2.CATPart
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

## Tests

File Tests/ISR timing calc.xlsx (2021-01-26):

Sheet: Sheet1
 |  |  |  |  |  |  | SM trigger setting
 |  |  |  |  |  |  | T | 10 | ms
 |  |  |  |  |  |  | F | 0.1 | KHz
cpu/IO clk | 8330000 | Hz | trial error | ISR tick mS | 10 |  |  | 100 | Hz
T0 prescaler div | 1024 |  |  | uS -> mS | 1000
clock for T0 (F) | 8134.765625 | Hz |  | clock for T0 (T) uS | 122.9291717 | uS | bit | prescalar | F (Hz) | T (ms)
 | 0.0001229291717 |  |  | value < 255 ! | 81.34765625 |  | 0 | 1 | 100.00 | 10
clock for T0 (T) | 122.9291717 | uS |  |  |  |  | 1 | 2 | 50.00 | 20
 |  |  |  |  |  |  | 2 | 4 | 25.00 | 40
 |  |  |  |  |  |  | 3 | 8 | 12.50 | 80
 |  |  |  | LED blink mS | 2500 |  | 4 | 16 | 6.25 | 160
Timer 2 with PWM |  |  |  | value < 65535 | 250 |  | 5 | 32 | 3.12 | 320
 |  |  |  |  |  |  | 6 | 64 | 1.56 | 640
N (prescaler div) | 1024 |  |  |  |  |  | 7 | 128 | 0.78 | 1280
Fpwm | 31.77642822 | Hz

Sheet: timing
 | T | T
 | ms
10 | 10
20
40 | 20
80
160 | 40
320
640 | 80
1280
 | e.g.
 | 80 pwm

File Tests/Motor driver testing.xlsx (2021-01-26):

 |  | L297 | NG |  |  | OK
3.49 | 1 | 20 | 4.97 | 3.46 | 1 | 20 | 4.97
0 | 2 | 19 | 0 | 0 | 2 | 19 | 0
0 | 3 | 18 | 2.55 | 0 | 3 | 18 | 2.55
0 | 4 | 17 | 0 | 2.21 | 4 | 17 | 0.47
4.39 | 5 | 16 | 2.63 | 4.44 | 5 | 16 | 2.6
4.37 | 6 | 15 | 1.15 | 2.22 | 6 | 15 | 1.23
0 | 7 | 14 | 0 | 2.22 | 7 | 14 | 0
4.42 | 8 | 13 | 0 | 4.4 | 8 | 13 | 0
0.7 | 9 | 12 | 5 | 2.22 | 9 | 12 | 5
5.09 | 10 | 11 | 0 | 5 | 10 | 11 | 0
 | L298
NG | 5ms period wave on pin 5,7
OK | 9ms period wave on pin 5,7

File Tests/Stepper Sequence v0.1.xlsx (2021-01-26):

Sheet: Sheet1
 |  |  |  |  |  |  |  |  |  |  |  |  |  | Lead colouring
 | Bipolar | A | B | C | D | x | x | A | B | C | D | x | x | Red | White | Blue | Green | Yellow | Black
 | Bipolar | a+ | b+ | a- | b- | x | x | a+ | b+ | a- | b- | x | x | A | A/C com | C | B | B/D com | D
 | Unipolar | 1a | 1b | 2a | 2b | a | b | 1a | 1b | 2a | 2b | a | b | 1a | a | 2a | 1b | b | 2b
 | Step no. | Unipolar |  |  |  |  |  | Bipolar
 | 1 | 1 | 0 | 0 | 0 |  |  | 1 | 0 | 0 | 0 | 8
Full step | 2 | 0 | 1 | 0 | 0 |  |  | 0 | 1 | 0 | 0 | 4
1 phase | 3 | 0 | 0 | 1 | 0 |  |  | 0 | 0 | 1 | 0 | 2
 | 4 | 0 | 0 | 0 | 1 |  |  | 0 | 0 | 0 | 1 | 1 |  |  | MCU | L298 i/p | L298 o/p | Motor lead
 |  |  |  |  |  |  |  |  |  |  |  | hex |  |  | PC.0 | IN1 (5) | OUT1 (2) | A
 | 1 | 1 | 0 | 0 | 1 |  |  | 1 | 0 | 0 | 1 | 9 |  |  | PC.1 | IN2 (7) | OUT2 (3) | B
Full step | 2 | 1 | 1 | 0 | 0 |  |  | 1 | 1 | 0 | 0 | C |  |  | PC.2 | IN3 (10) | OUT3 (13) | C
2 phase | 3 | 0 | 1 | 1 | 0 |  |  | 0 | 1 | 1 | 0 | 6 |  |  | PC.3 | IN4 (12) | OUT4 (14) | D
 | 4 | 0 | 0 | 1 | 1 |  |  | 0 | 0 | 1 | 1 | 3
 | 1 | 1 | 0 | 0 | 1 |  |  | 1 | 0 | 0 | 1 | 9
Half step | 2 | 1 | 0 | 0 | 0 |  |  | 1 | 0 | 0 | 0 | 8
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

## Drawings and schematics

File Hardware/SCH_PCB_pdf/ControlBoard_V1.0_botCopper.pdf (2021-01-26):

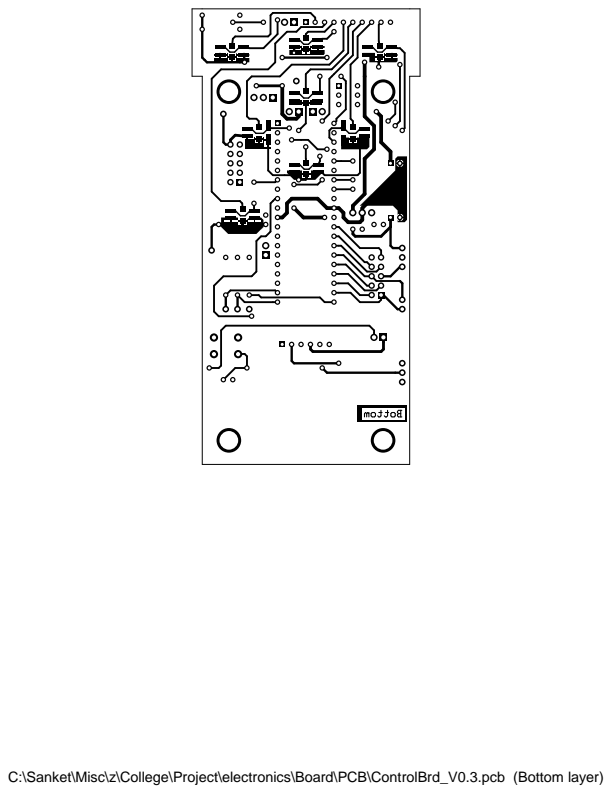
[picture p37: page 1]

C:\Sanket\Misc\z\College\Project\electronics\Board\PCB\ControlBrd_V0.3.pcb (Bottom layer)

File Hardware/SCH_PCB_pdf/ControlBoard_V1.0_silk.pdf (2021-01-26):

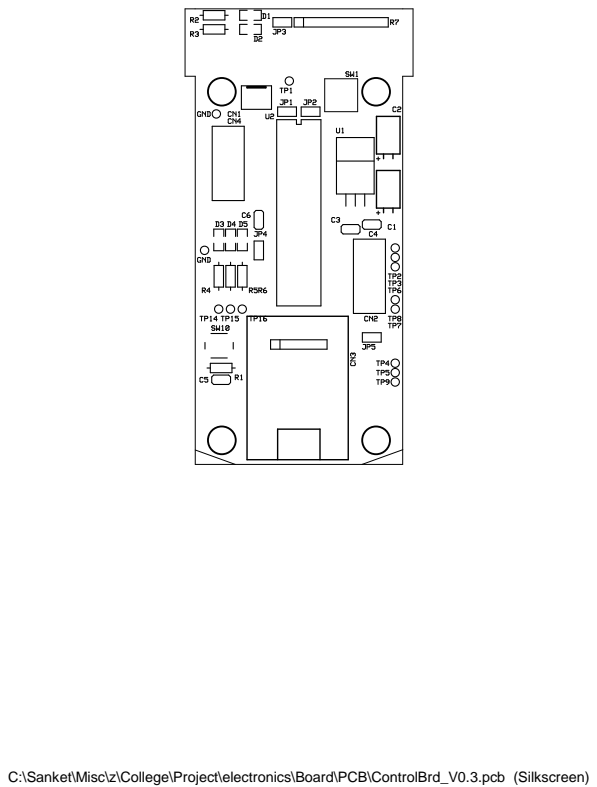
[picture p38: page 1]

C:\Sanket\Misc\z\College\Project\electronics\Board\PCB\ControlBrd_V0.3.pcb (Silkscreen)

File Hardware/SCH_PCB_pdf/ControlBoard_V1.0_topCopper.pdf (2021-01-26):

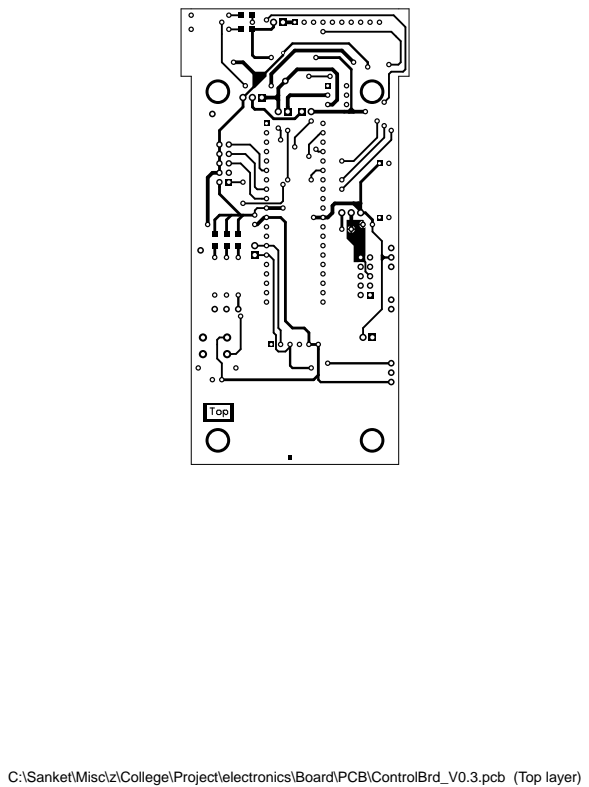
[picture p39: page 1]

C:\Sanket\Misc\z\College\Project\electronics\Board\PCB\ControlBrd_V0.3.pcb (Top layer)

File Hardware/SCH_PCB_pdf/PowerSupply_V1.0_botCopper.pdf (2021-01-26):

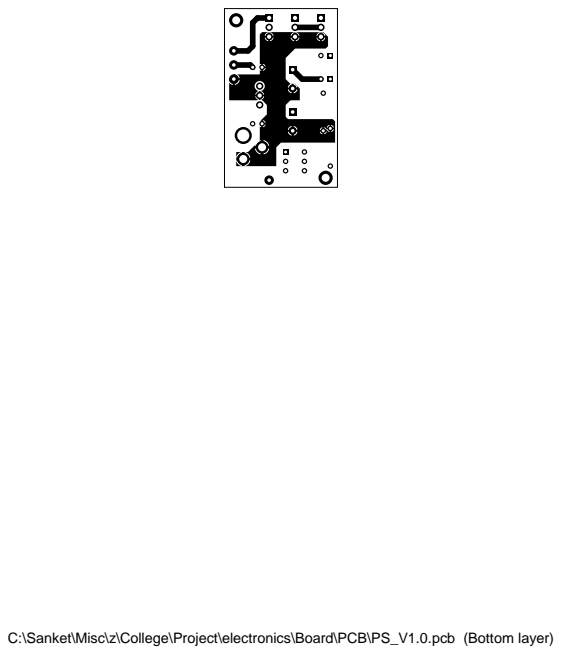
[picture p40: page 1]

C:\Sanket\Misc\z\College\Project\electronics\Board\PCB\PS_V1.0.pcb (Bottom layer)

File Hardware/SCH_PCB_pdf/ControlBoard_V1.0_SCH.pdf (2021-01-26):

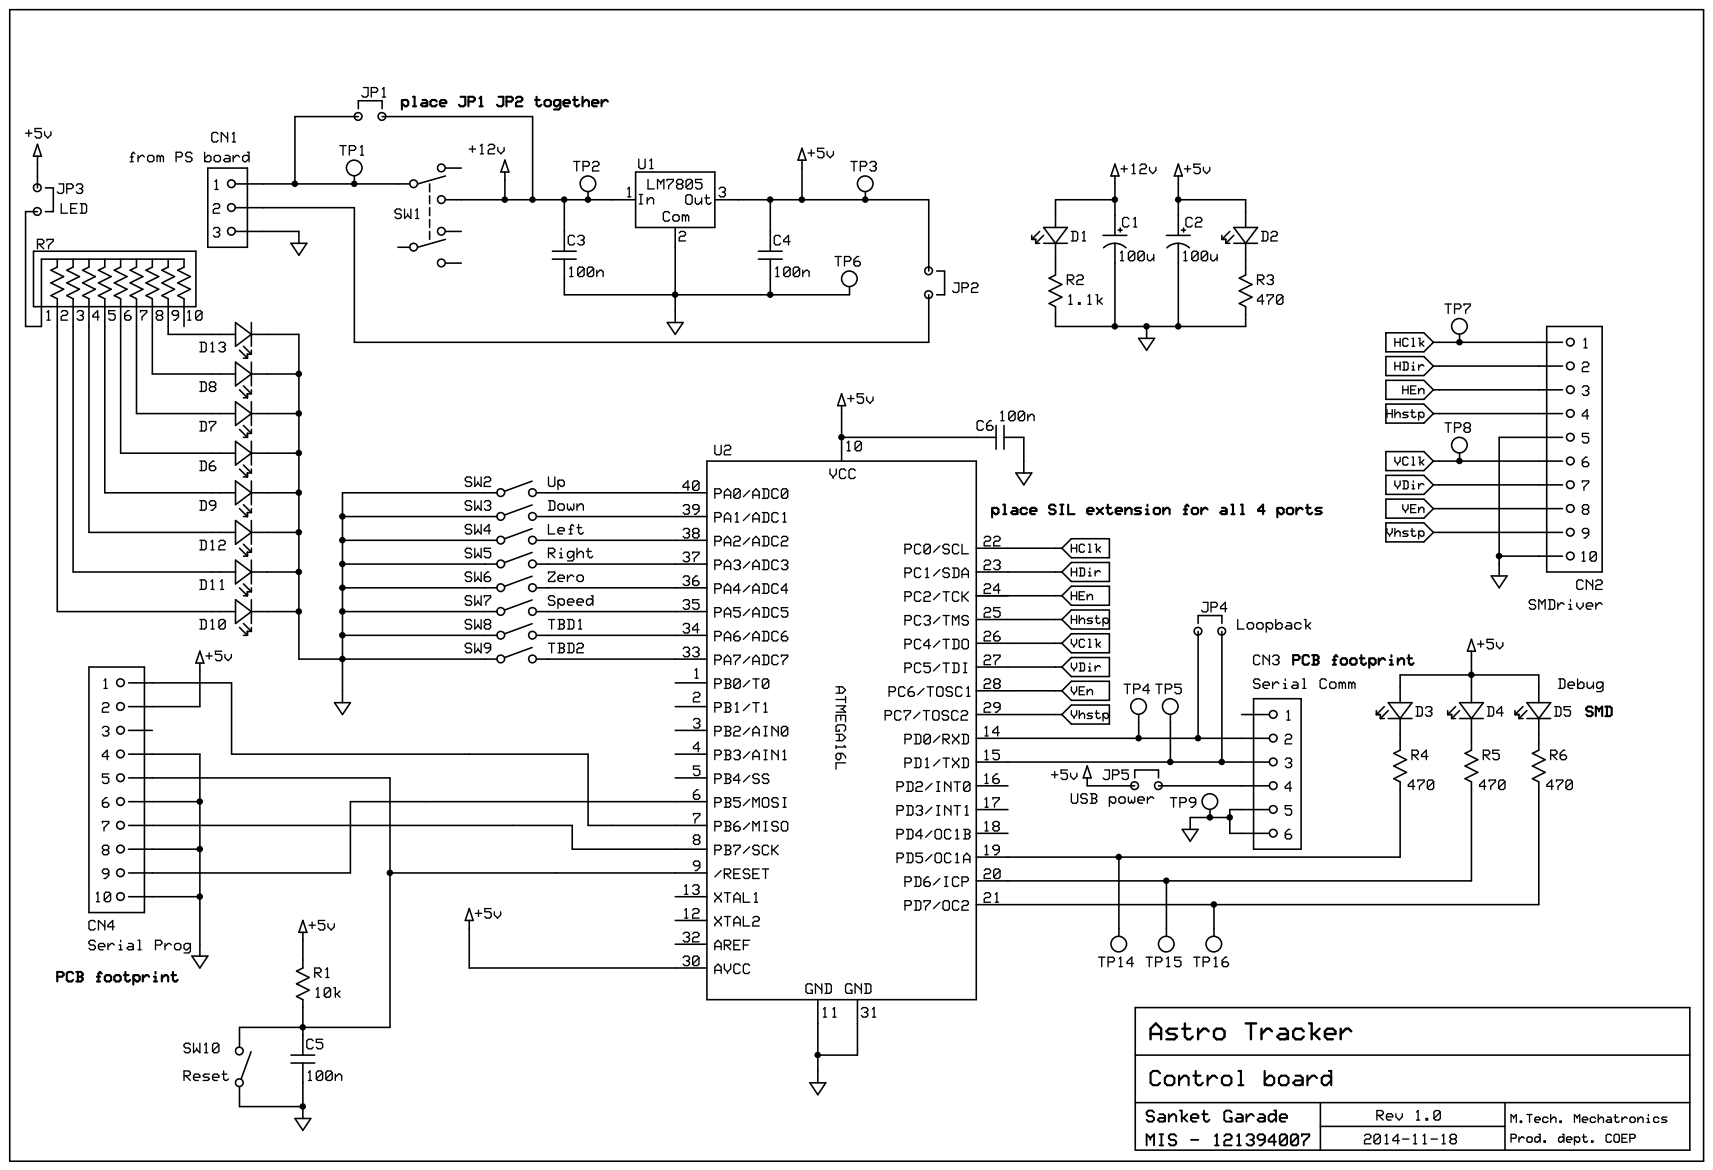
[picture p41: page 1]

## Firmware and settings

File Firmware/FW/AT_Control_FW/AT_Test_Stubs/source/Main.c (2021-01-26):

/************************ Includes ************************/

#include <avr/interrupt.h>
#include "C:\Users\Vedashree\Documents\AVRStudio\AT_Control_FW\AT_Test_Stubs\include/Common.h"

/************************ Global variables ************************/

volatile uint32_t	gu32TimeTicks		= 0;
//volatile uint32_t	gu32Time100msTicks	= 0;

// Request
uint8_t gu8ReqStart			= FALSE;
uint8_t gu8ReqSpeedRef		= 0x00;
uint8_t gu8ReqMode			= MODE_NORMAL;
uint8_t gu8ReqDirectionH	= 0;
uint8_t gu8ReqDirectionV	= 0;
uint16_t gu16ReqPulseTargetH= 0;
uint16_t gu16ReqPulseTargetV= 0;
uint8_t gu8ReqZeroSet		= 0;
uint8_t gu8ReqQuadrantSet	= 1;
uint16_t gu16ReqDegreesSetH	= 0;
uint16_t gu16ReqDegreesSetV	= 0;

// Response
uint16_t gu16PulseElapsedH	= 0;
uint16_t gu16PulseElapsedV	= 0;
uint16_t gu16DegreesElapsedH= 0;
uint16_t gu16DegreesElapsedV= 0;


/************************ Function declarations ************************/



/************************ Function definitions ************************/


void main(void)
{
	//Initialize the hardware
	rvHardwareInit();
	
	H_ENABLE;
	
	H_DIR_CLOCKWISE;

	V_ENABLE;
	
	V_DIR_CLOCKWISE;

	
	//Infinite loop
	while(1)
	{
		rvReadRequest();
		rvSendResponse();
	}
	
}



/*	This is the interrupt service routine for TIMER0 Compare Match Interrupt.
	ISR frequency : 100 usec */
ISR(TIMER0_COMP_vect)
{
	static uint16_t lu16ISRDivCounter = 0;

		
#if 0	
	rvMotorTest();
#endif
	
	if(TRUE == gu8ReqStart)
	{
		// data Rx is time in 1ms multiple. (0~255)
		// used to clock the motor and LED
		if(lu16ISRDivCounter > (gu8ReqSpeedRef * 10))
		{
			LED3_TOGGLE;
	
			H_CLK_TOGGLE;
	
			V_CLK_TOGGLE;
	
	

	
			lu16ISRDivCounter = 0;
		}
	}

	rvTxSerialData();
	
	lu16ISRDivCounter++;

	// Increment global tick
	gu32TimeTicks++;


}



// Test stub to test both motors - Run CW - Stop - Run CCW
void rvMotorTest(void)
{
	static uint16_t lu16TestStubCounter = 0;

	if((lu16TestStubCounter > 0) && (lu16TestStubCounter <= 20000))
	{
		H_ENABLE;
		H_DIR_ANTICLOCKWISE;

		V_ENABLE;
		V_DIR_CLOCKWISE;
		
		LED1_ON;
		LED2_OFF;
	} 
	else if((lu16TestStubCounter > 20000) && (lu16TestStubCounter <= 25000))
	{
		H_DISABLE;
		V_DISABLE;

		LED1_OFF;
		LED2_OFF;
	}
	if((lu16TestStubCounter > 25000) && (lu16TestStubCounter <= 45000))
	{
		H_ENABLE;
		H_DIR_CLOCKWISE;

		V_ENABLE;
		V_DIR_ANTICLOCKWISE;
		
		LED1_OFF;
		LED2_ON;
	} 
	else if((lu16TestStubCounter > 45000) && (lu16TestStubCounter <= 50000))
	{
		H_DISABLE;
		V_DISABLE;
		
		LED1_OFF;
		LED2_OFF;
	}
	else if (lu16TestStubCounter > 50000)
	{
		lu16TestStubCounter = 0;
	}
	
	lu16TestStubCounter++;

}

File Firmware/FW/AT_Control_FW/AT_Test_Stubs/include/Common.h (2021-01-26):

/*
 * Common.h
 *
 * Created: 10/2/2014 3:47:58 PM
 *  Author: Sanket
 */ 


#ifndef COMMON_H_
#define COMMON_H_


#include <avr/io.h>


#define TRUE	1
#define FALSE	0

#define B7		7
#define B6		6
#define B5		5
#define B4		4
#define B3		3
#define B2		2
#define B1		1
#define B0		0




/*************** ISR related ***************/
#define ISR_TICK_US				100		//Timer ISR period (for high priority jobs) (in micro sec.)
#define ISR_TIMER_CLOCK_US		8		//NG-> approx 122uS after prescaler (CPU clk = 8.33 MHz found by trial error experiment)
#define ISR_TICK_VALUE			(uint8_t)(((uint32_t)ISR_TICK_US)/ISR_TIMER_CLOCK_US)


/*************** Time in 100 us ticks ***************/
#define T_100MS					1000	// 100u x 1000 = 100ms
#define T_200MS					2000	// 100u x 2000 = 200ms

/*************** UART related ***************/

#define FOSC1 8000000
#define BAUD 9600
#define MYUBRR FOSC1/16/BAUD-1

/*************** LED Blink related ***************/
#define LED_BLINK_MS			(uint16_t)500	// blink rate of LED in mSec
#define LED_BLINK_INTERVAL		(uint16_t)((uint16_t)LED_BLINK_MS / (uint16_t)ISR_TICK_MS)

/*************** I/O related ***************/

#define PORT_PU_D				(SFIOR |= (1<<PUD))
#define PORT_PU_E				(SFIOR &= ~(1<<PUD))

#define MOTOR_PORT_OUT			PORTC
#define MOTOR_PORT_IN			PINC
#define MOTOR_PORT_DIR			DDRC

#define LAMP_PORT_OUT			PORTD
#define LAMP_PORT_IN			PIND
#define LAMP_PORT_DIR			DDRD


#define SW_PORT_OUT				PORTA
#define SW_PORT_IN				PINA
#define SW_PORT_DIR				DDRA

/*************** Port operations related ***************/

/*** LED ***/

#define LED1_OFF				LAMP_PORT_OUT|=(1<<B5)
#define LED2_OFF				LAMP_PORT_OUT|=(1<<B6)
#define LED3_OFF				LAMP_PORT_OUT|=(1<<B7)

#define LED1_ON					LAMP_PORT_OUT&=~(1<<B5)
#define LED2_ON					LAMP_PORT_OUT&=~(1<<B6)
#define LED3_ON					LAMP_PORT_OUT&=~(1<<B7)

#define LED1_TOGGLE				LAMP_PORT_OUT^=(1<<B5)
#define LED2_TOGGLE				LAMP_PORT_OUT^=(1<<B6)
#define LED3_TOGGLE				LAMP_PORT_OUT^=(1<<B7)

/*** Stepper Motor Interface ***/

/*** Horizontal Motion ***/
#define H_CLK_TOGGLE			MOTOR_PORT_OUT^=(1<<B0)		// Clock

#define H_DIR_CLOCKWISE			MOTOR_PORT_OUT|=(1<<B1)		// Direction
#define H_DIR_ANTICLOCKWISE		MOTOR_PORT_OUT&=~(1<<B1)	// 1 : CW , 0 : CCW

#define H_ENABLE				MOTOR_PORT_OUT|=(1<<B2)		// Enable
#define H_DISABLE				MOTOR_PORT_OUT&=~(1<<B2)	// 1 : En , 0 : Dis

#define H_STEP_HALF				MOTOR_PORT_OUT|=(1<<B3)		// Step size
#define H_STEP_FULL				MOTOR_PORT_OUT&=~(1<<B3)	// 1 : Half , 0 : Full

/*** Vertical Motion ***/
#define V_CLK_TOGGLE			MOTOR_PORT_OUT^=(1<<B4)		// Clock

#define V_DIR_CLOCKWISE			MOTOR_PORT_OUT|=(1<<B5)		// Direction
#define V_DIR_ANTICLOCKWISE		MOTOR_PORT_OUT&=~(1<<B5)	// 1 : CW , 0 : CCW

#define V_ENABLE				MOTOR_PORT_OUT|=(1<<B6)		// Enable
#define V_DISABLE				MOTOR_PORT_OUT&=~(1<<B6)	// 1 : En , 0 : Dis

#define V_STEP_HALF				MOTOR_PORT_OUT|=(1<<B7)		// Step size
#define V_STEP_FULL				MOTOR_PORT_OUT&=~(1<<B7)	// 1 : Half , 0 : Full


/*************** Serial Comm related ***************/
#define COMM_SOF				0x55
#define COMM_EOF				0xAA


// Frame IDs - Request
#define REQ_START_STOP			0x11
#define REQ_SPEED				0x12
#define REQ_MODE				0x13
#define REQ_DIRECTION			0x14
#define REQ_PULSE_COUNT			0x15
#define REQ_ZERO				0x16
#define REQ_QUADRANT			0x17
#define REQ_DEGREES				0x18

// Frame IDs - Response
#define  RESP_SYS_STATUS		0x21
#define  RESP_PULSE_COUNT		0x25
#define  RESP_QUADRANT			0x27
#define  RESP_DEGREES			0x28


/*************** Application related ***************/
// Operation Modes
#define MODE_NORMAL				0
#define MODE_SCAN				1


/*************** Enums ***************/

typedef enum
{
	RX_SOF_WAIT = 0,
	RX_SOF_READ,
	RX_FRAME_NO_READ,
	RX_DLC_READ,
	RX_DATA_READ,
	RX_CHKSUM_READ,
	RX_EOF_READ	
}RX_FRAME_READ_STATES;


/*************** Variables related ***************/

extern volatile uint32_t gu32TimeTicks;

extern uint8_t gau8RxBuffer[16];
extern uint8_t gau8TxBuffer[16];
extern uint8_t gu8TxPtr;
extern uint8_t gu8TxPtrTarget;

extern uint8_t gu8SendQuadrantResp;
extern uint8_t gu8SerialTxDone;


// Request
extern uint8_t gu8ReqStart;
extern uint8_t gu8ReqSpeedRef;
extern uint8_t gu8ReqMode;
extern uint8_t gu8ReqDirectionH;
extern uint8_t gu8ReqDirectionV;
extern uint16_t gu16ReqPulseTargetH;
extern uint16_t gu16ReqPulseTargetV;
extern uint8_t gu8ReqZeroSet;
extern uint8_t gu8ReqQuadrantSet;
extern uint16_t gu16ReqDegreesSetH;
extern uint16_t gu16ReqDegreesSetV;


// Response
extern uint16_t gu16PulseElapsedH;
extern uint16_t gu16PulseElapsedV;
extern uint16_t gu16DegreesElapsedH;
extern uint16_t gu16DegreesElapsedV;



#endif /* COMMON_H_ */
